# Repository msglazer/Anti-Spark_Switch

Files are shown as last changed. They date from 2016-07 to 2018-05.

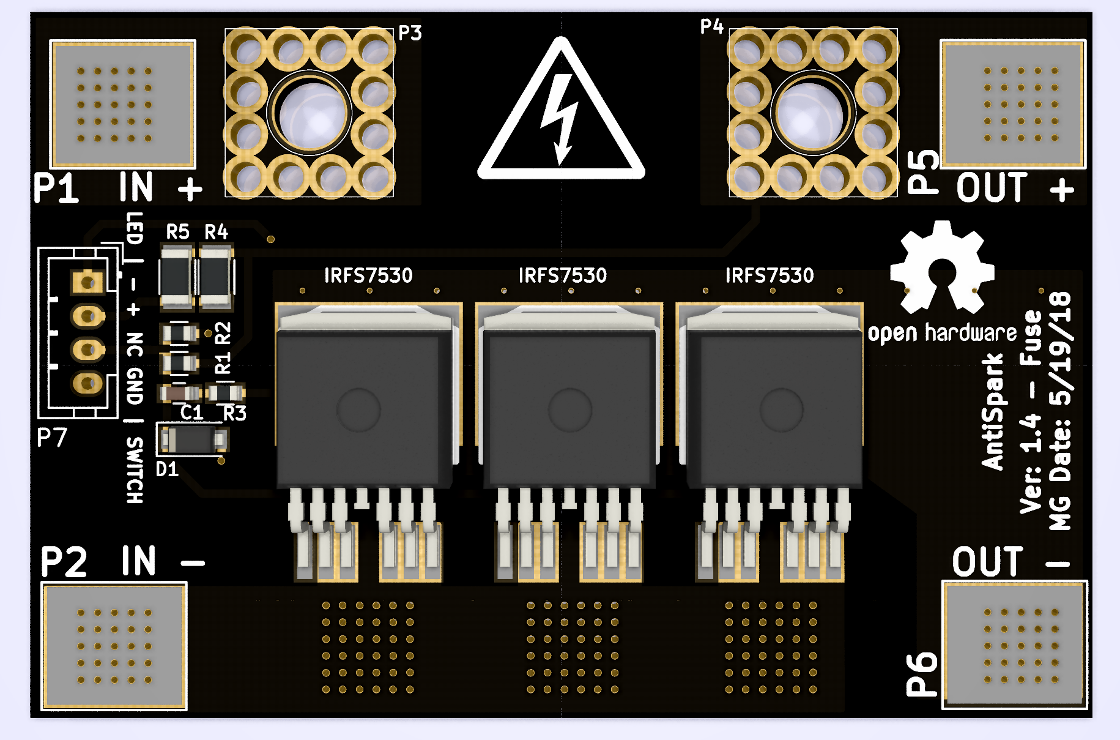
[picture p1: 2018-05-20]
Documentation/images/V1_4_Fuse.PNG

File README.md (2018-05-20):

# Anti Spark Switch
Personal improvements/changes to the vedder antispark switch

Design allows for a battery to be connected to a source without the usual spark in the connector, also provides a convenient on off ability.
Improvements to the design include an upgraded, more robust fuse and fuse holder, an additional MOSFET for higher current handling as well as
better distribution of power through the MOSFETs. There is also the option of adding an LED powered through the PCB, the LED is powered after the MOSFET switch

There are two versions currently, with fuse and without fuse. The without fuse version is located in its own branch, master contains the fuse version

schematic2
front2
back2

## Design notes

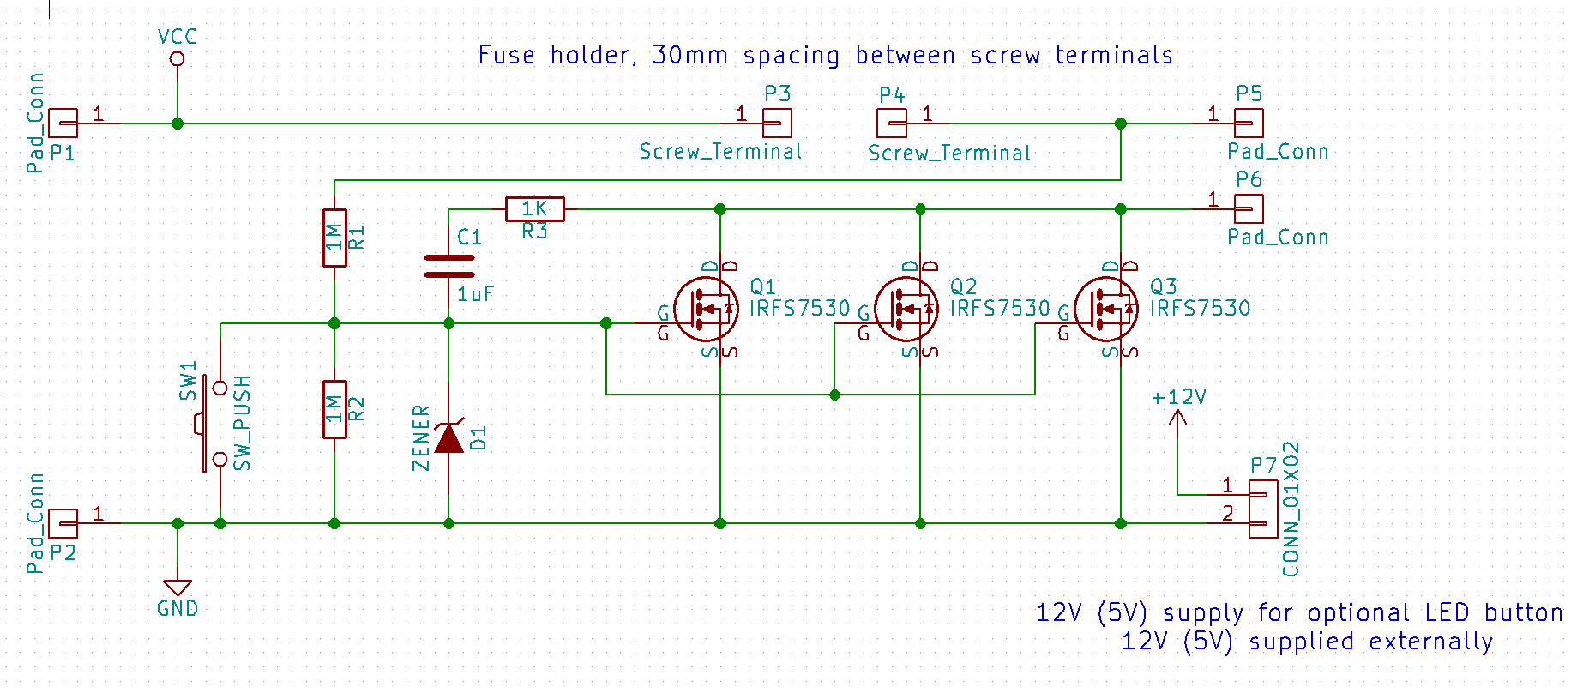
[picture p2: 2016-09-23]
Documentation/images/Schematic2.PNG

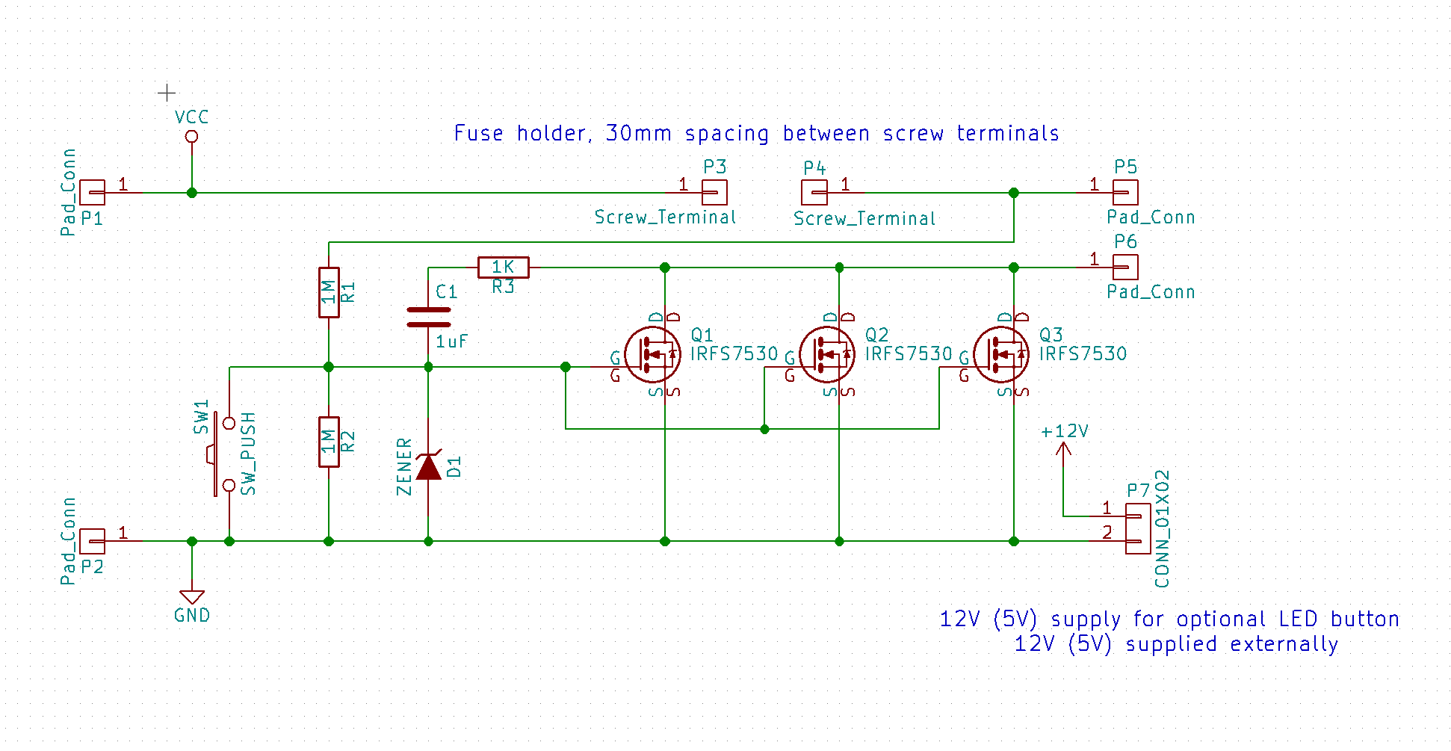
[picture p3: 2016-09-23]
Documentation/images/Schematic.PNG

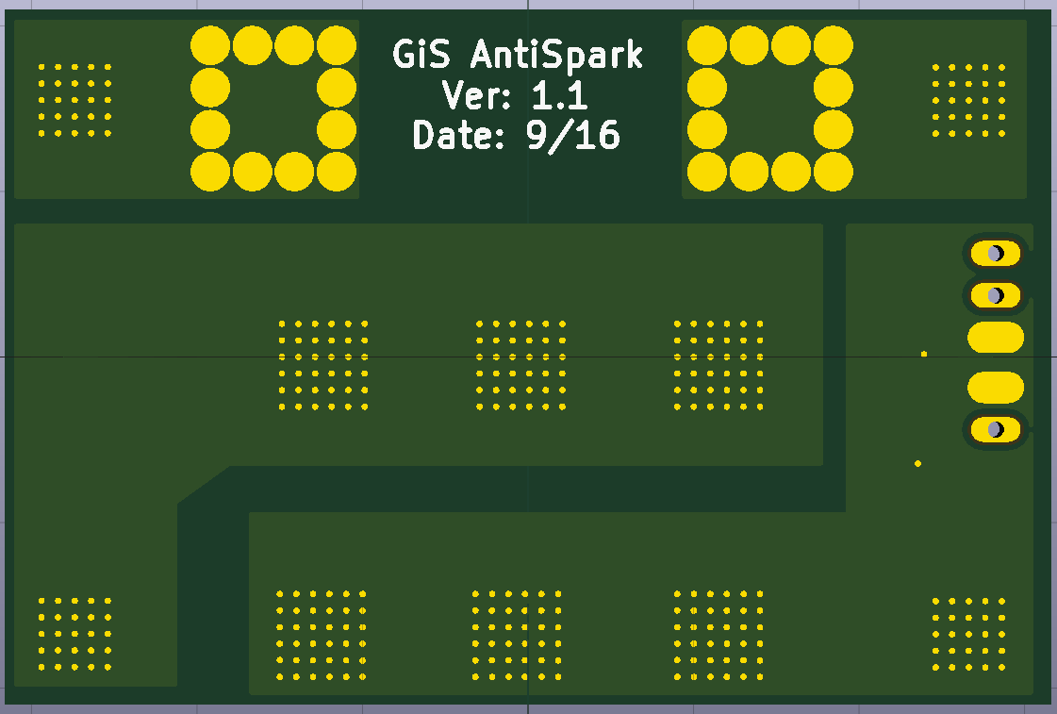
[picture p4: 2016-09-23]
Documentation/images/Back2.PNG

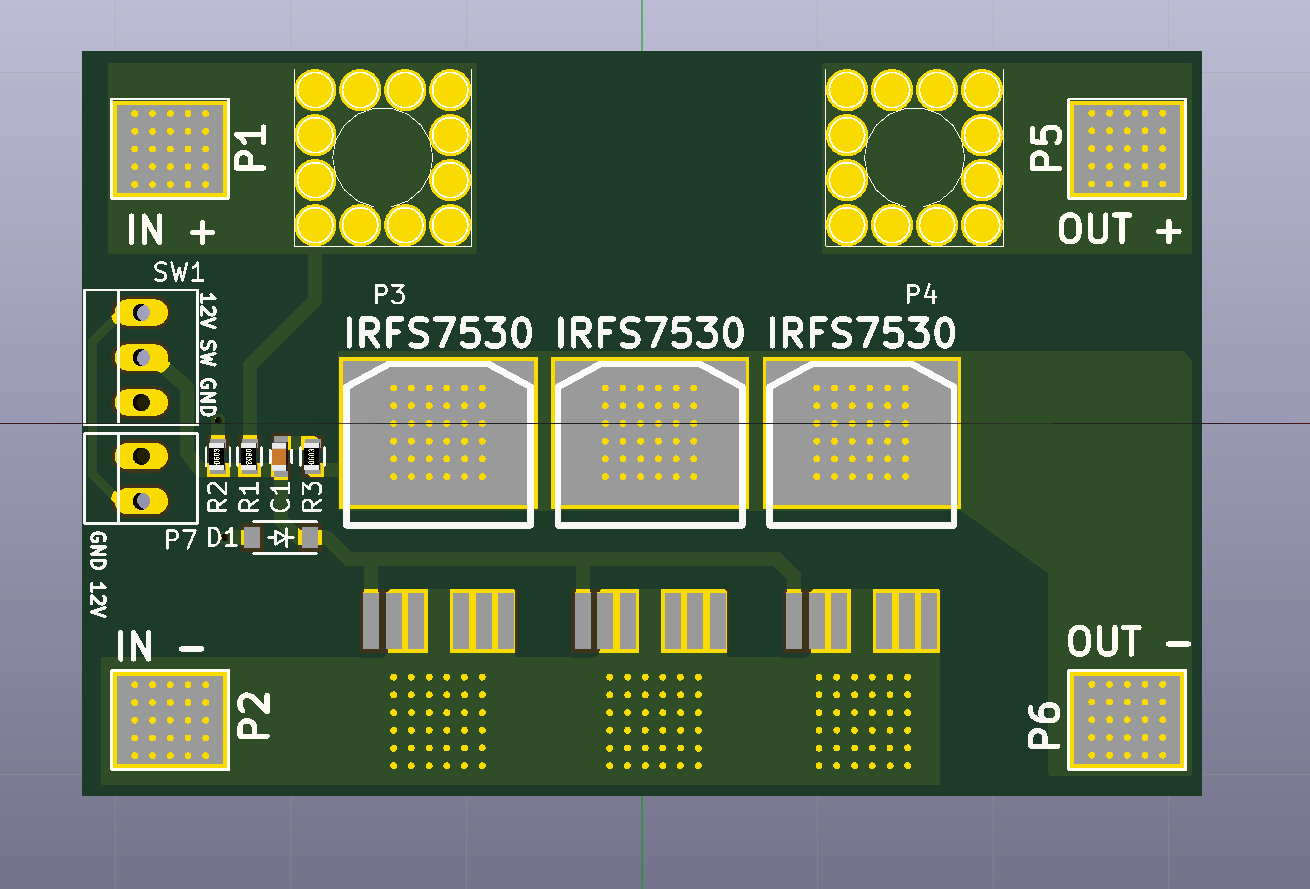
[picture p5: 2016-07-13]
Documentation/images/Front.PNG

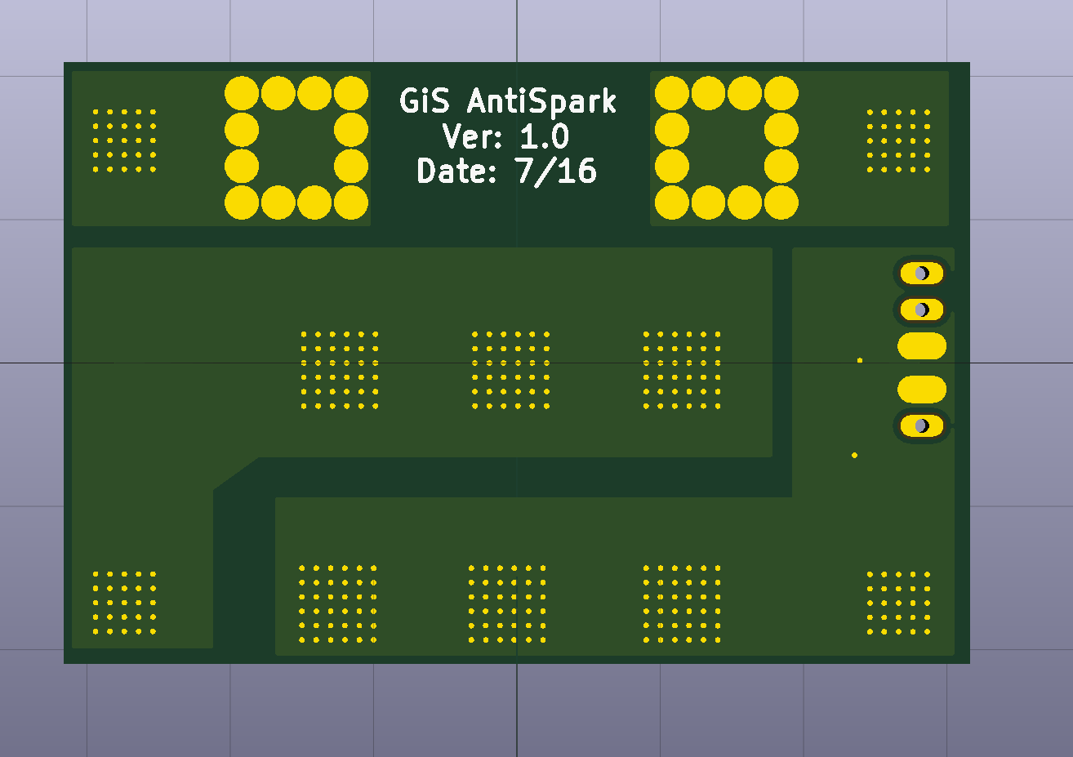
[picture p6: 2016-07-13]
Documentation/images/Back.PNG

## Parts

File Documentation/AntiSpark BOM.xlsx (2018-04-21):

Bill of Materials (BOM) - Anti_Spark_Switch
Item # | Qty | Ref Des | Manufacturer | Mfg Part # | Dist. Part # | Price Per Unit | Total Price | Description | Package | Type | Datasheet | Notes
1 | 3 | Q1,Q2,Q3 | Infineon Technologies | IRFS7530TRL7PP | 942-IRFS7530TRL7PP | $3.65 | $10.95 | Power MOSFET | D2PAK-7 | SMD | http://www.mouser.com/ds/2/196/irfs7530-7ppbf-937822.pdf
2 | 2 | R1,R2 | Panasonic | ERJ-3EKF1004V | 667-ERJ-3EKF1004V | $0.15 | $0.30 | 1M Resistor | 0603 | SMD | http://www.mouser.com/ds/2/315/AOA0000C86-911473.pdf
3 | 1 | R3 | Panasonic | ERJ-3EKF1001V | 667-ERJ-3EKF1001V | $0.15 | $0.15 | 1K Resistor | 0603 | SMD
4 | 2 | R4,R5 |  |  |  | $0.15 | $0.30 | 16.5K Resistor | 1206 | SMD
5 | 1 | C1 | AVX | 06033C105KAT2A | 581-06033C105KAT2A | $0.11 | $0.11 | 1uF Capacitor | 0603 | SMD
6 | 1 | D1 | Taiwan Semiconductor | BZT52B12 | 821-BZT52B12 | $0.15 | $0.15 | 12V Zener Diode | SOD-123 | SMD
7 | 2 | P3,P4 | Wurth Electronics | 7460408 | 710-7460408 | $3.89 | $7.78 | M5 Threaded Power Terminal | M5 Thread | Thru Hole | http://www.mouser.com/ds/2/445/7460408-538106.pdf
8 | 1 | F1 | Littelfuse | 142.5631.5702 | 576-142.5631.5702 | $3.30 | $3.30 | 70A Slow Blow Auto Fuse | Fuse | Bolt Down | http://www.mouser.com/ds/2/240/Littelfuse_BF1_58V_Datasheet-523203.pdf
 |  |  |  |  | Board Multiplier: | 1 | Mainboard Total:
 |  |  |  |  |  |  | $23.04
 |  |  |  |  |  |  | Grand Total:
 |  |  |  |  |  |  | $23.04

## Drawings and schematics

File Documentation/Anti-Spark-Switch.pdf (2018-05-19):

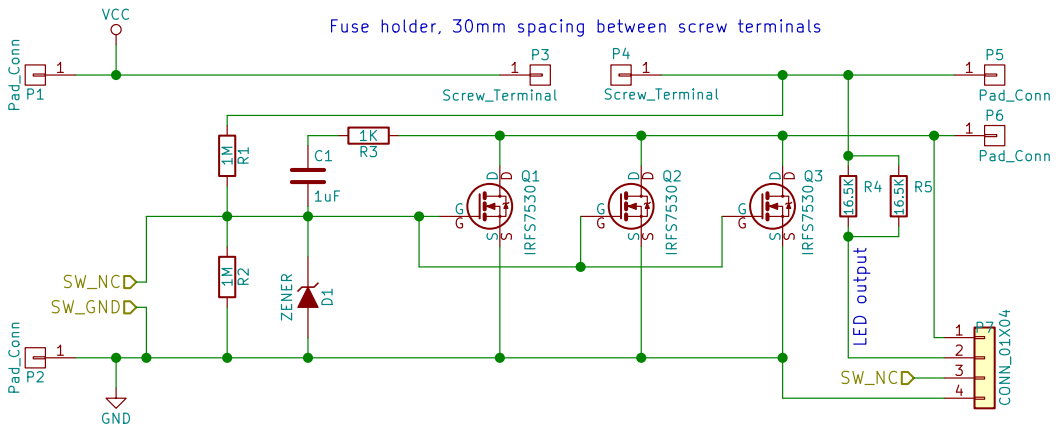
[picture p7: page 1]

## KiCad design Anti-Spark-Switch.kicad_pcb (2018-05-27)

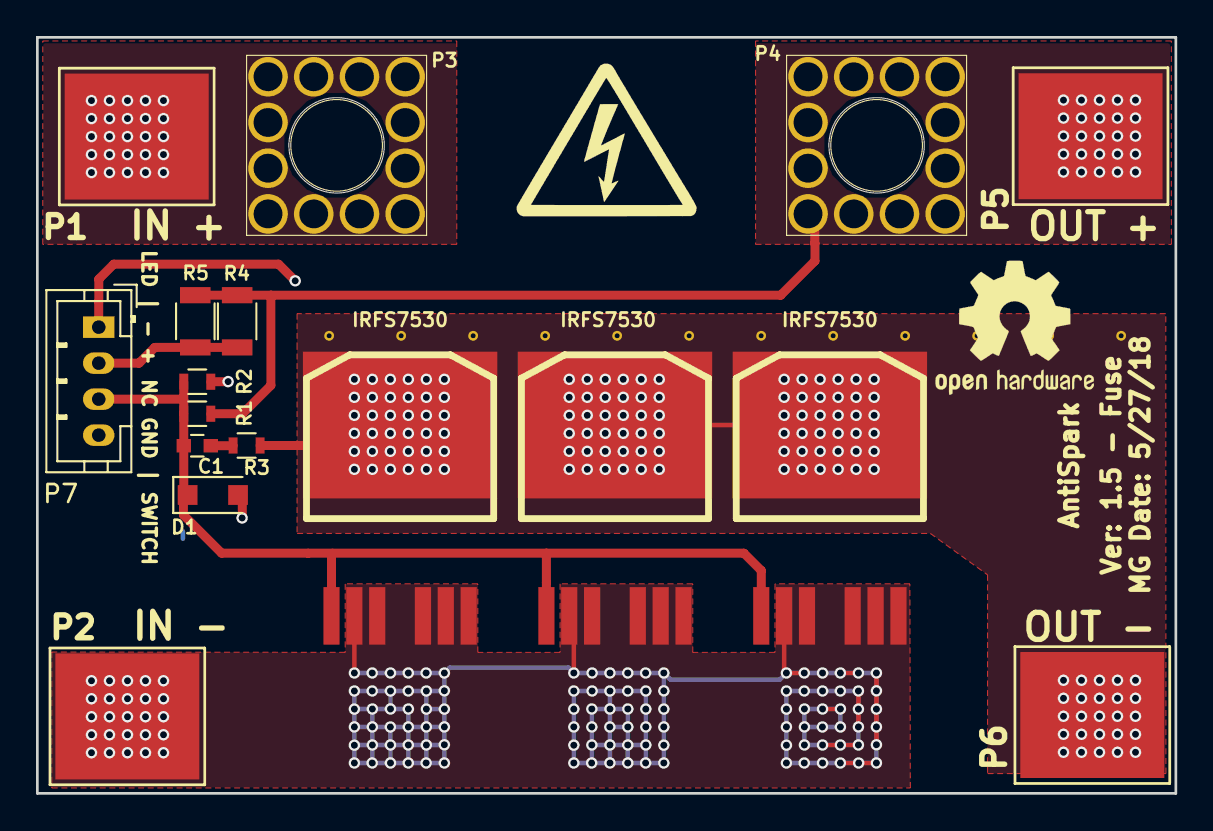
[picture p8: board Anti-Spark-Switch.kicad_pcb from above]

Board: 2 copper layers, 63.2 x 42.0 mm, 17 parts (0 on the bottom side), 7 nets.

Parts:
C1: 1uF; C_0603
D1: ZENER; D_SOD-123F
P1, P2, P5, P6: Pad_Conn; 1PAD_8x7mm
P3, P4: Screw_Terminal; M5_Screw_Terminal_12_pin
P7: CONN_01X04; JST_PH_B4B-PH-K_1x04_P2.00mm_Vertical
Q1, Q2, Q3: IRFS7530; D2PAK-7-GDS
R1, R2: 1M; R_0603
R3: 1K; R_0603
R4, R5: 16.5K; R_1206

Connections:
/SW_NC: C1.2, D1.1, P7.3, Q1.G, Q2.G, Q3.G, R1.2, R2.1
GND: D1.2, P2.1, P7.4, Q1.S, Q2.S, Q3.S, R2.2
unnamed: C1.1, R3.2
unnamed: P4.1, P5.1, R1.1, R4.1, R5.1
unnamed: P6.1, P7.1, Q1.D, Q2.D, Q3.D, R3.1
unnamed: P7.2, R4.2, R5.2
VCC: P1.1, P3.1

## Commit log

2016-07-01 initial commit, schematic 90% done
    [Anti-Spark-Switch.kicad_pcb, Anti-Spark-Switch.sch]
2016-07-07 schematic completed, PCB started
    [Anti-Spark-Switch.kicad_pcb, Anti-Spark-Switch.sch]
2016-07-08 continued work on PCB
    [Anti-Spark-Switch.kicad_pcb]
2016-07-13 finalized rev 1 PCB, generated gerbers, captured images
    [Anti-Spark-Switch-B.Cu.gbr, Anti-Spark-Switch-B.Mask.gbr, Anti-Spark-Switch-B.SilkS.gbr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]
2016-07-15 updated BOM, shifted schematic
    [Anti-Spark-Switch.sch, AntiSpark BOM.xlsx]
2016-07-19 gerber update
    [Anti-Spark-Switch-B.Cu.gbr, Anti-Spark-Switch-B.Mask.gbr, Anti-Spark-Switch-B.SilkS.gbr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]
2016-08-10 changed fuse value
    [AntiSpark BOM.xlsx]
2016-09-20 Rev 1.1 changes
    Moved Gate power input from before to after fuse for improved safety
    [Anti-Spark-Switch.kicad_pcb, Anti-Spark-Switch.sch]
2016-09-23 Text changes to schematic
    [Anti-Spark-Switch.sch]
2016-09-23 minor Rev 1.1 changes
    [Anti-Spark-Switch.kicad_pcb]
2016-09-23 text fixes/passive component footprint changes
    [Anti-Spark-Switch.sch]
2016-09-23 updated gerbers
    [Anti-Spark-Switch-B.Cu.gbr, Anti-Spark-Switch-B.Mask.gbr, Anti-Spark-Switch-B.SilkS.gbr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]
2016-09-23 BOM update
    [AntiSpark BOM.xlsx]
2016-09-23 updated a footprint, fixed reference numbers
    [Anti-Spark-Switch.kicad_pcb]
2016-09-23 slight change to through hole diameter
2017-02-12 Fixed short through LED issue
    may still need some tweaking
    [Anti-Spark-Switch.kicad_pcb, Anti-Spark-Switch.sch]
2018-04-19 updated schematic, changed bom slightly
    [Anti-Spark-Switch.sch, AntiSpark BOM.xlsx]
2018-04-19 moved images to new folder, updated a PCB footprint
    [Anti-Spark-Switch.sch, AntiSpark BOM.xlsx]
2018-04-21 V1.3 Gerbers
    [Anti-Spark-Switch-B.Cu.gbr, Anti-Spark-Switch-B.Mask.gbr, Anti-Spark-Switch-B.SilkS.gbr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]
2018-04-21 updated the PCB per new schematic changes and general improvements
    [Anti-Spark-Switch.kicad_pcb]
2018-04-21 schematic changes and updating the netlist
    [Anti-Spark-Switch.sch]
2018-04-21 potential drill issue
    [Anti-Spark-Switch.kicad_pcb]
2018-04-21 updated the gerber zip file
2018-05-19 updated gerber files
    [Anti-Spark-Switch-B.Cu.gbr, Anti-Spark-Switch-B.Mask.gbr, Anti-Spark-Switch-B.Paste.gbr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]
2018-05-19 current version schematic pdf
2018-05-19 changed connector to JST-PH-4 vertical connector, added silkscreen stuff
    [Anti-Spark-Switch.kicad_pcb, Anti-Spark-Switch.sch]
2018-05-19 fixed silkscreen issue
    [Anti-Spark-Switch.kicad_pcb]
2018-05-20 improved the PCB a bit
    [Anti-Spark-Switch.kicad_pcb]
2018-05-27 updated the gerbers
    [Anti-Spark-Switch-B.Cu.gbr, Anti-Spark-Switch-B.Mask.gbr, Anti-Spark-Switch-B.Paste.gbr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]
2018-05-27 PCB has been updated per a fixed screw terminal component
    [Anti-Spark-Switch.kicad_pcb]
2018-05-27 updated the gerbers, change is V1.5 now
    [Anti-Spark-Switch-B.Cu.gbr, Anti-Spark-Switch-B.Mask.gbr, Anti-Spark-Switch-B.Paste.gbr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]
